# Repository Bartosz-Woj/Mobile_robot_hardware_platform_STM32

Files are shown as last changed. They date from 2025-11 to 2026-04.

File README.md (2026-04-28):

# Mobile robot hardware platform

## Project Description

**Universal PCB** with STM32G431 with two 2 h-bridges and input/output connectors designed for usage as mobile robot mainboard. The PCB can be use as mainboard for mini sumo robot, balancing robot, linefollower and other similar projects.

## Main functionality

- high range of power suply voltage (recommended: 9-12V PSU or 2S-3S Li-Po)
- STM32G431
- IR receiver
- power lines: 3V3, 5V, 6V5 with step-down converters.
- switch for enabling/disabling power lines
- 2x i2C connector
- 2x servo connector
- 2x encoder connector
- 2x H-bridge (3.6A each)
- 2x 10pin IDC connector
- 1x 16pin IDC connector [for IR distance sensor](https://github.com/Bartosz-Woj/Modulated_infrared_distance_sensor)
- connector for IR sumo [robot start module](https://p1r.se/startmodule/)

## Program uploading and debugging

The ST-link can be connected to the J2 connector by IDC wire to [ST-Link Nucleo board programming shield] (https://github.com/Bartosz-Woj/ST_LINK-Nucleo-programming-shield) or to the connector J6 by goldpin wires.

## Software

In the folder /software there are example projects made in STM32CubeIDE which can be used for hardware testing and for initial configuration:

- initial_configuration - project with initial configuration of CubeMX. In the main function there is code for testing PWM.

## Project status

- electronic desing: finished
- example usage design: on going

## Additional modules

- [ST-Link Nucleo board programming shield](https://github.com/Bartosz-Woj/ST_LINK-Nucleo-programming-shield)
- [Modulated infrared distance sensor module which peak detection](https://github.com/Bartosz-Woj/Modulated_infrared_distance_sensor)

## Usage in mobile robot projects

- [Low cost mini sumo robot](https://github.com/Bartosz-Woj/Mini-sumo-robot)

## Photos

- **Schematic:**  
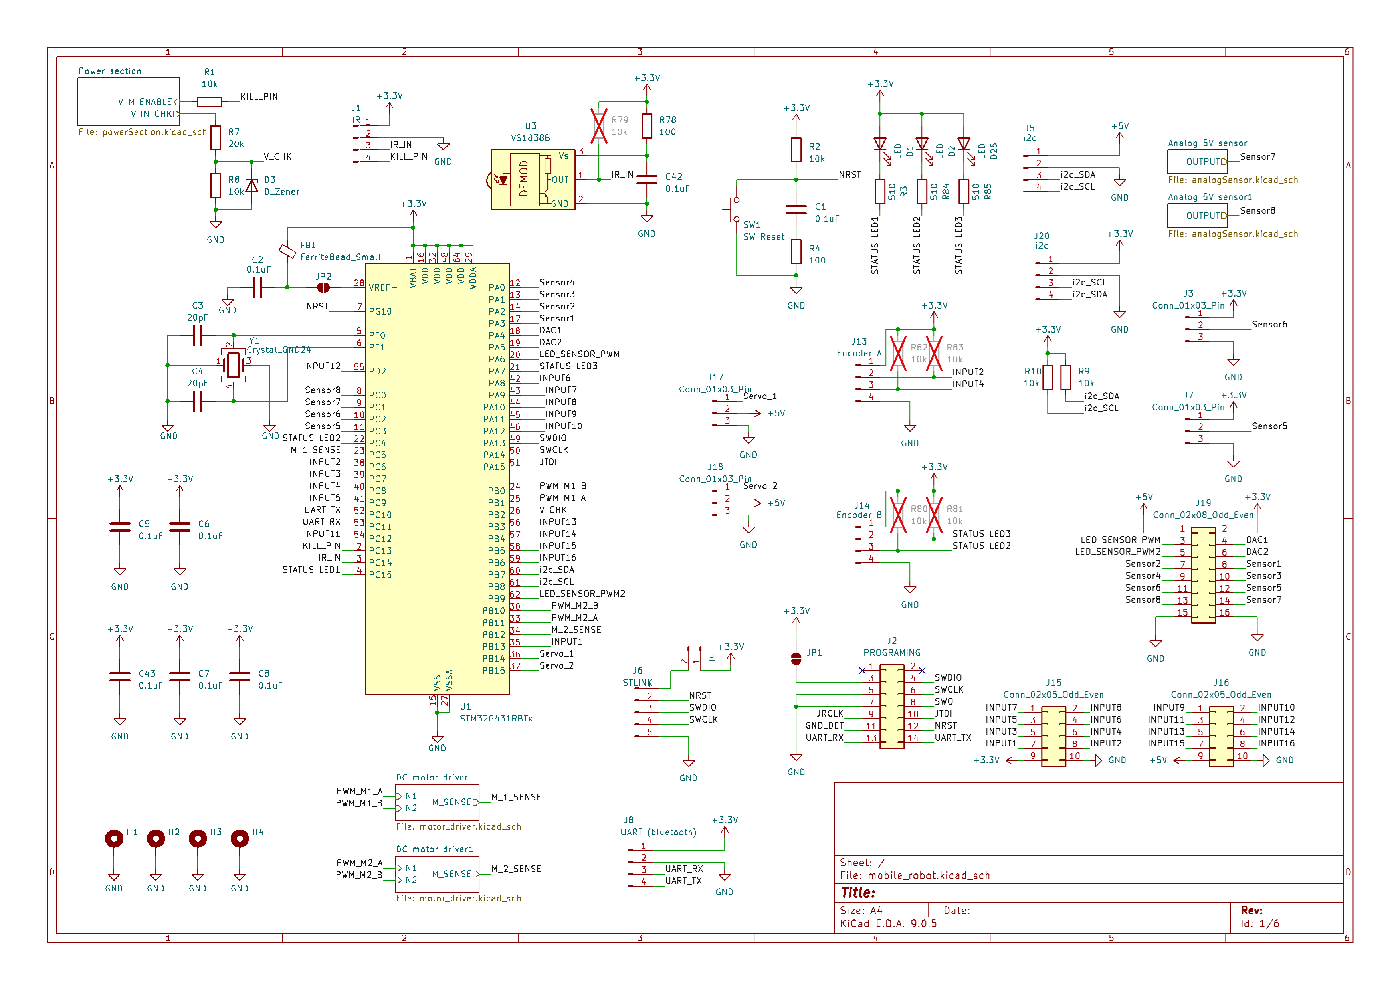
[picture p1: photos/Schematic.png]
Schematic
  
- **PCB top side:**  
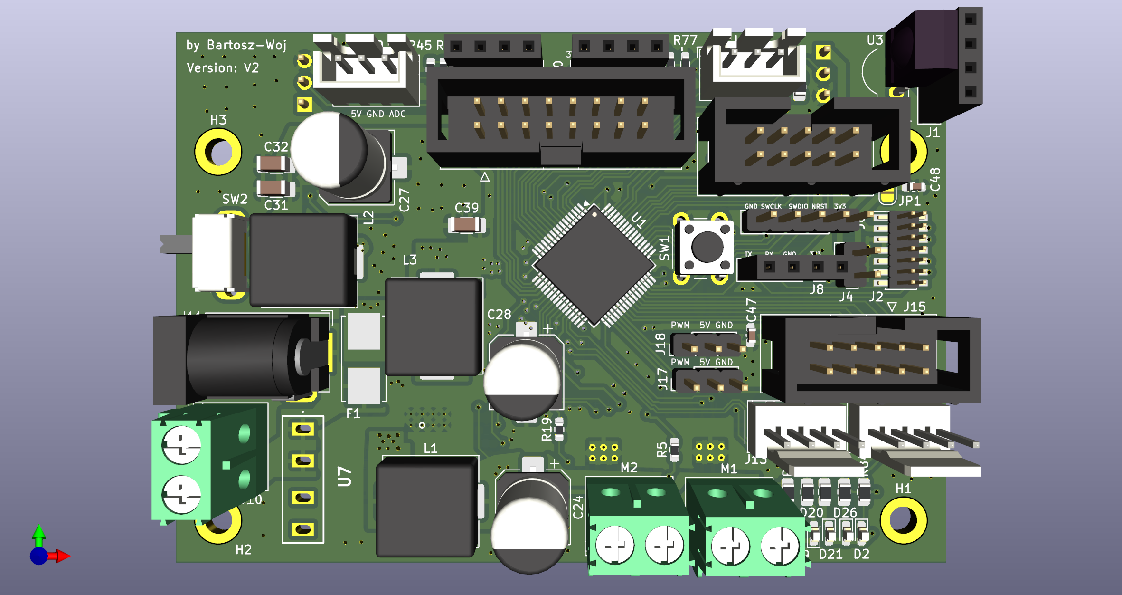
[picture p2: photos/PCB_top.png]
PCB top side
  
- **PCB bottom side:**  
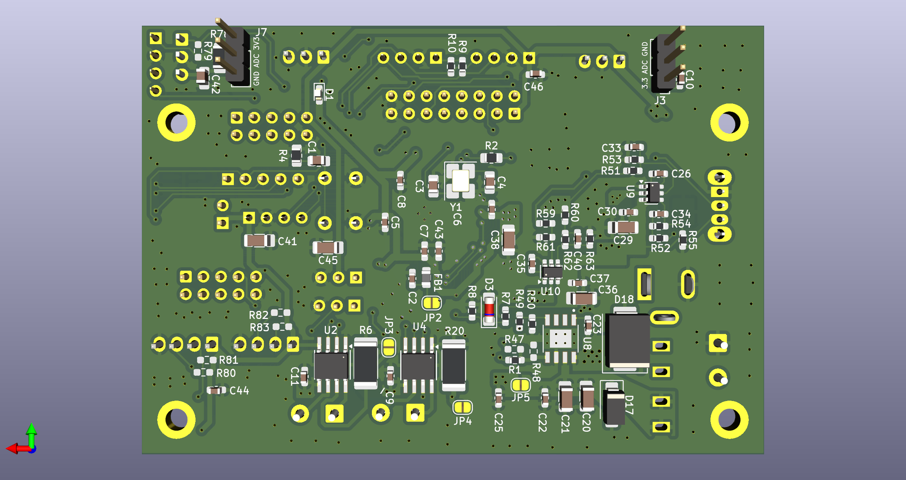
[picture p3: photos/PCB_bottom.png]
PCB bottom side
  

- **Debuging mode:**  
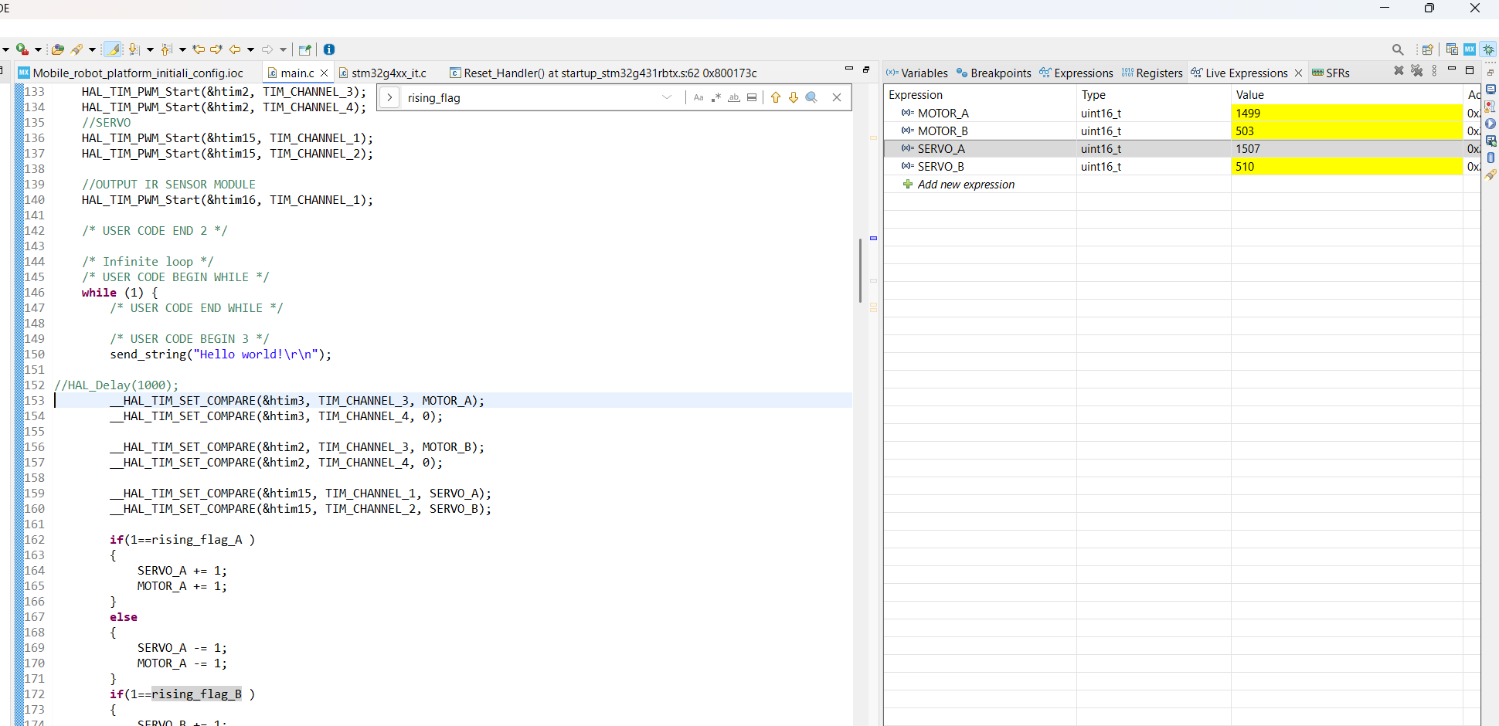
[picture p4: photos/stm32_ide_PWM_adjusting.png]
Debuging mode in STM32CubeIDE
  

- **Example connection with motors**  
  Connection with motors

---

## Author

- **Project by:** Bartosz-Woj (Bartosz Wojciechowski)
- **Date:** 10.11.2025

---

## License

Licensed under the **CERN Open Hardware License v2 – Permissive (CERN-OHL-P)**  
You are free to **use, modify, and redistribute** this project, provided that you **credit the original author**.

## Changelog

- V1 - initial release
- V2 - minor improvments: modified U3 footprint, rotated J7, updated routing (microcontroller, power section)

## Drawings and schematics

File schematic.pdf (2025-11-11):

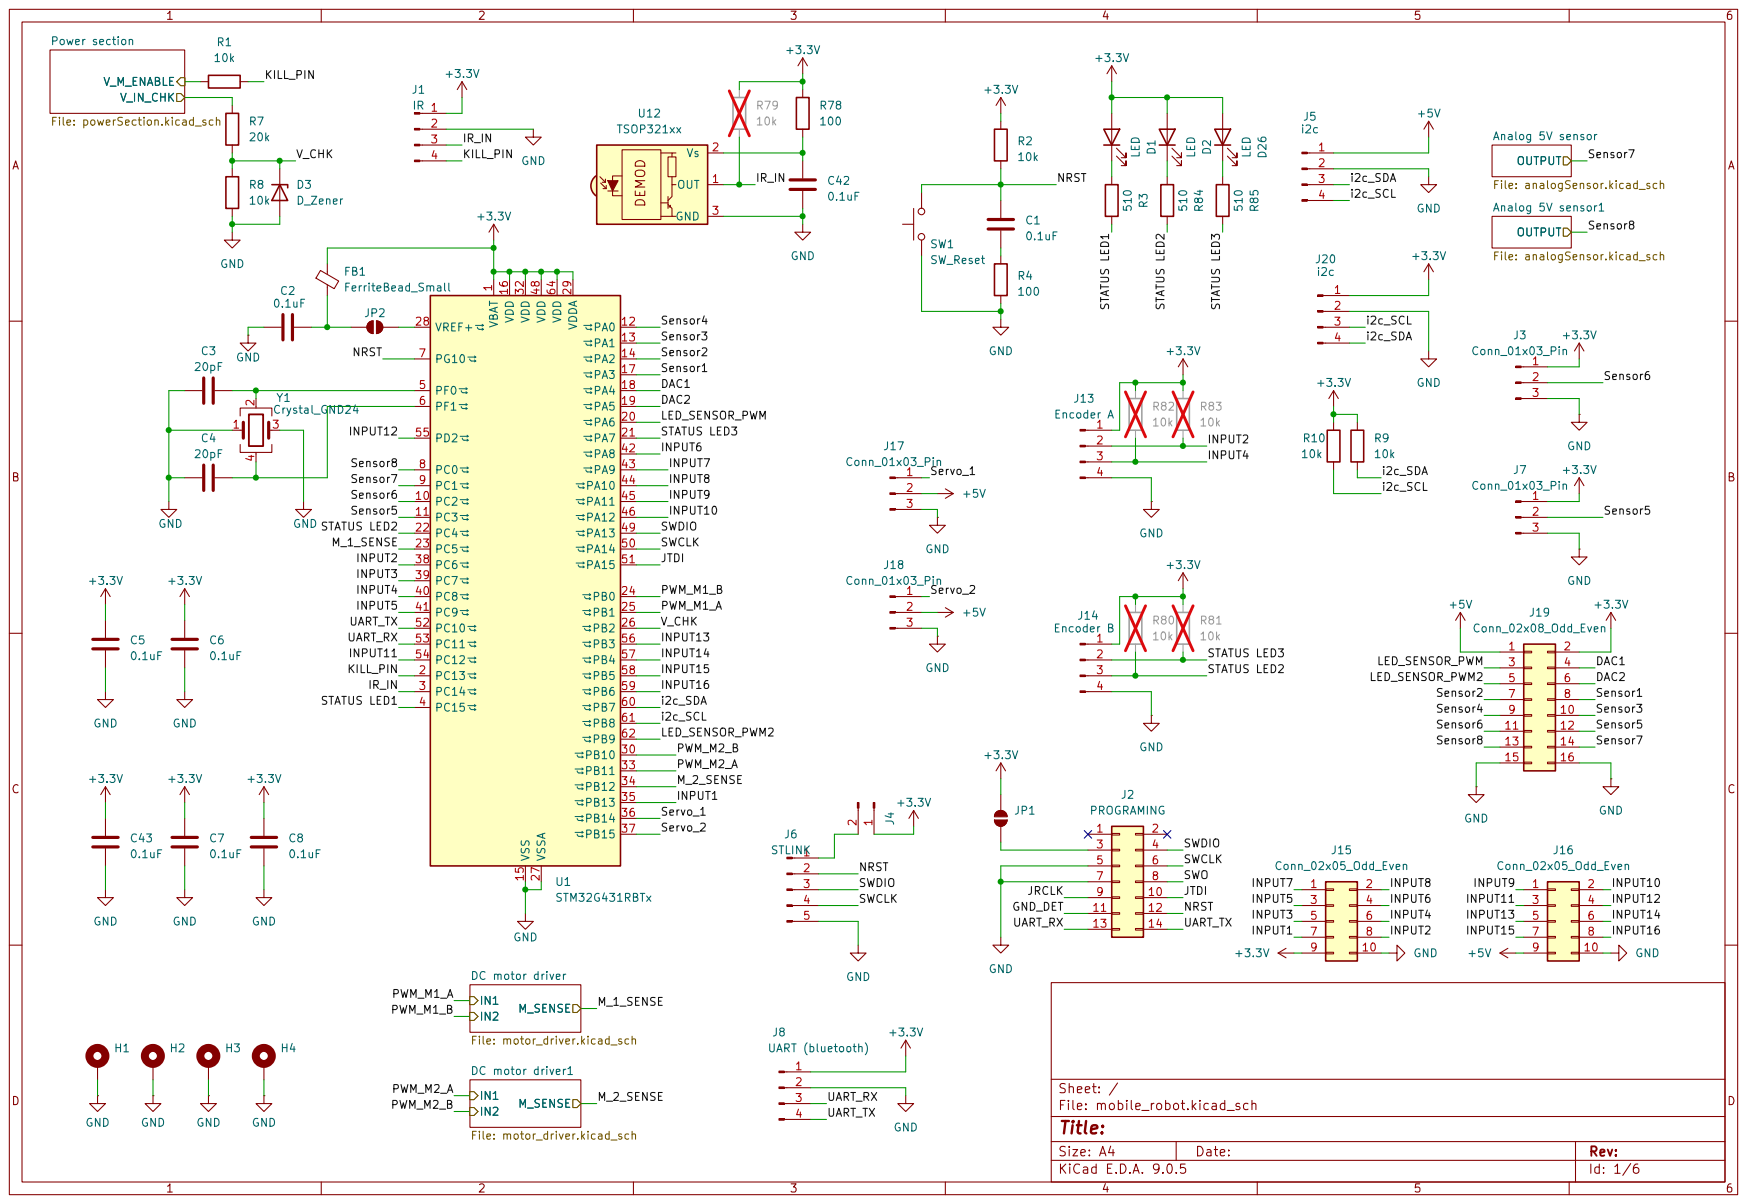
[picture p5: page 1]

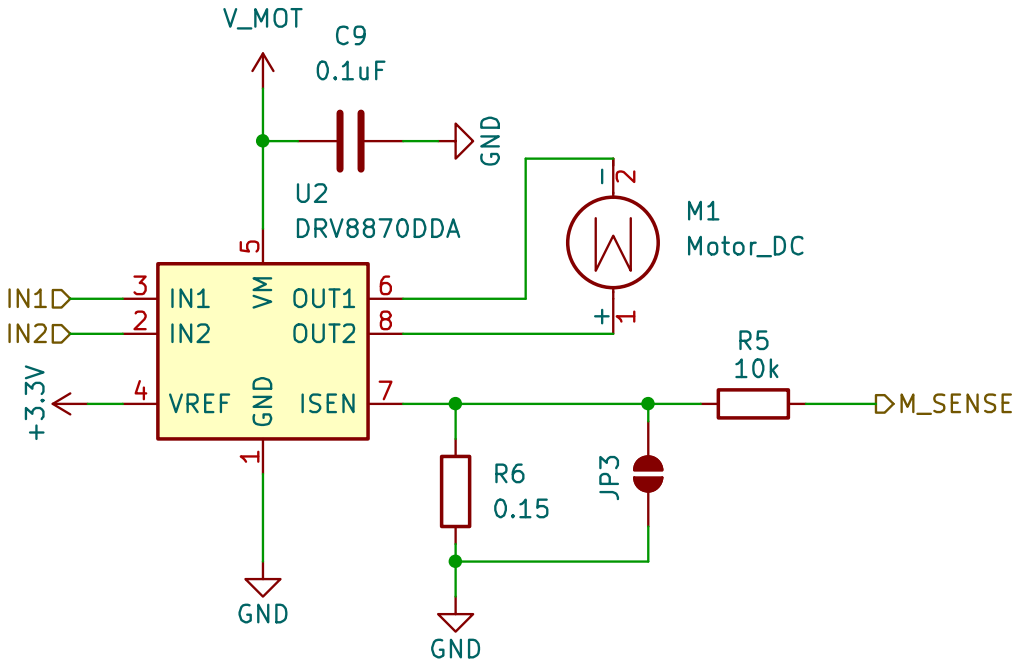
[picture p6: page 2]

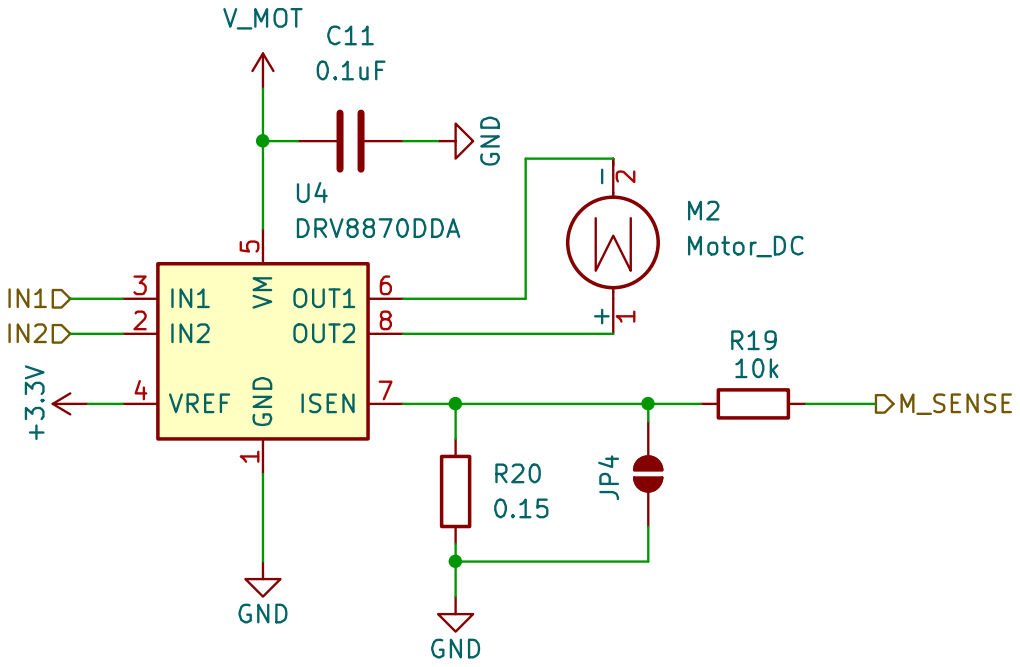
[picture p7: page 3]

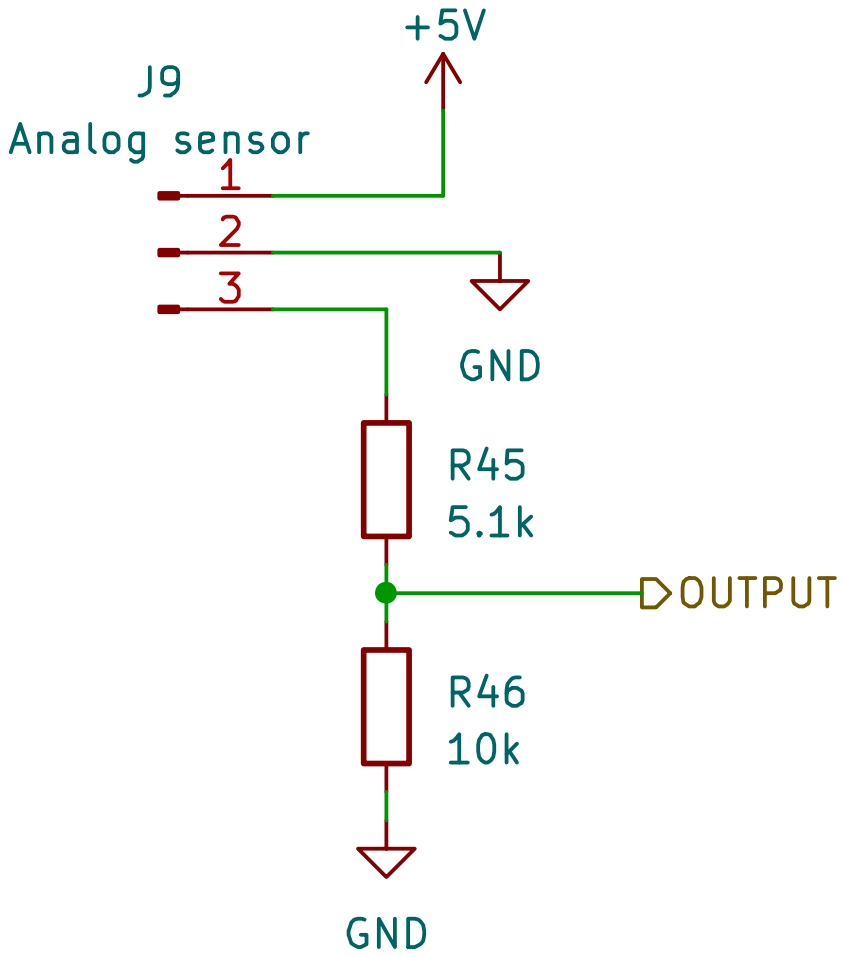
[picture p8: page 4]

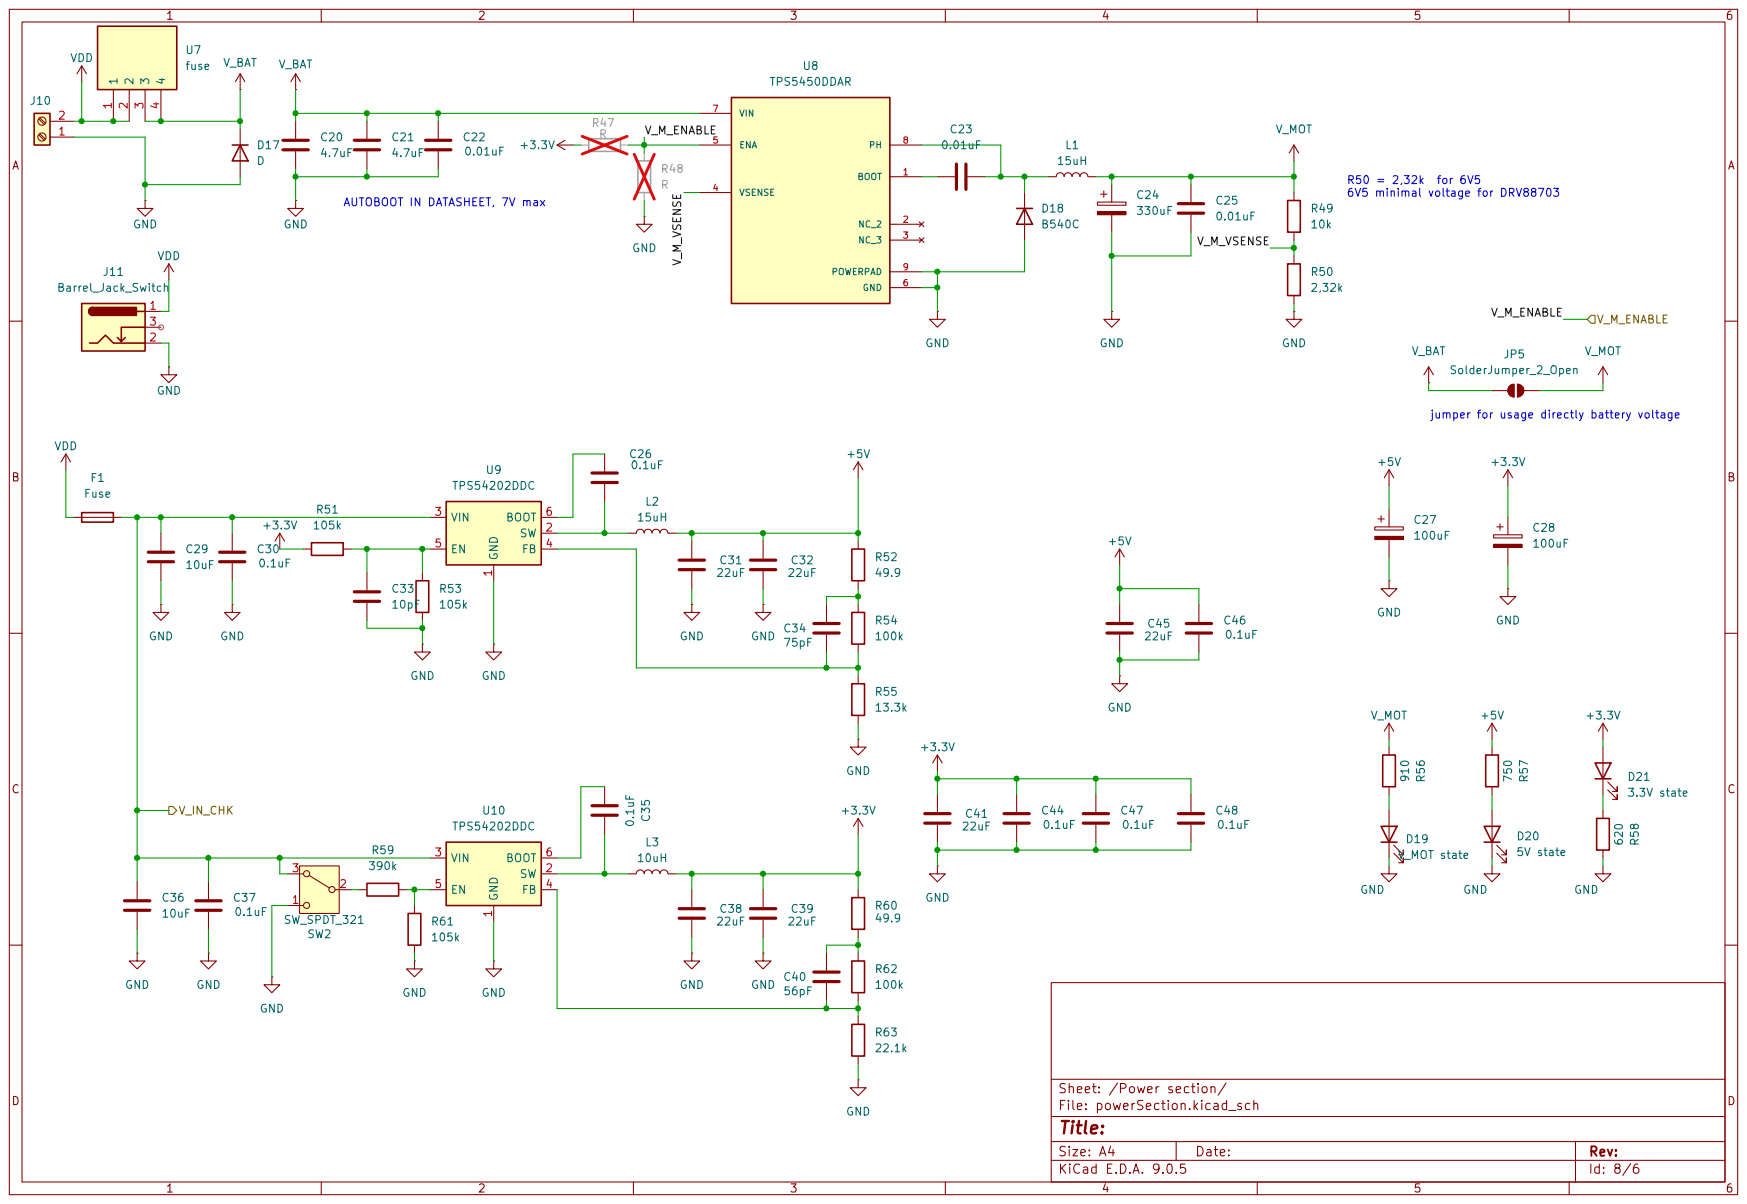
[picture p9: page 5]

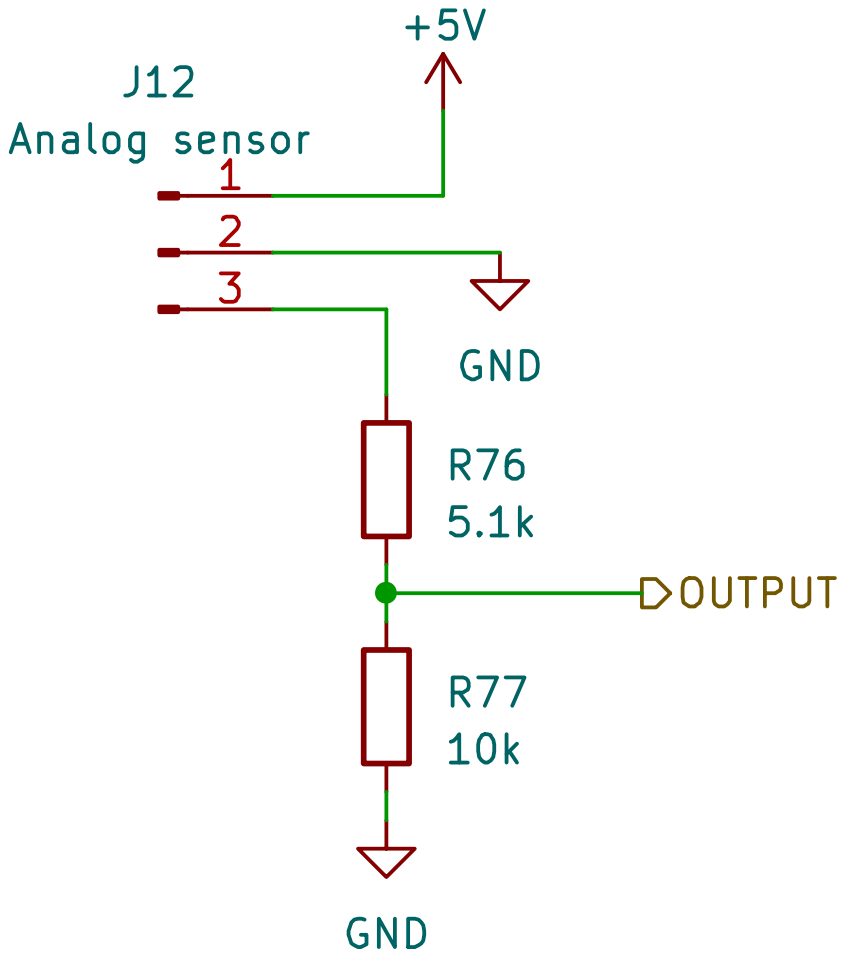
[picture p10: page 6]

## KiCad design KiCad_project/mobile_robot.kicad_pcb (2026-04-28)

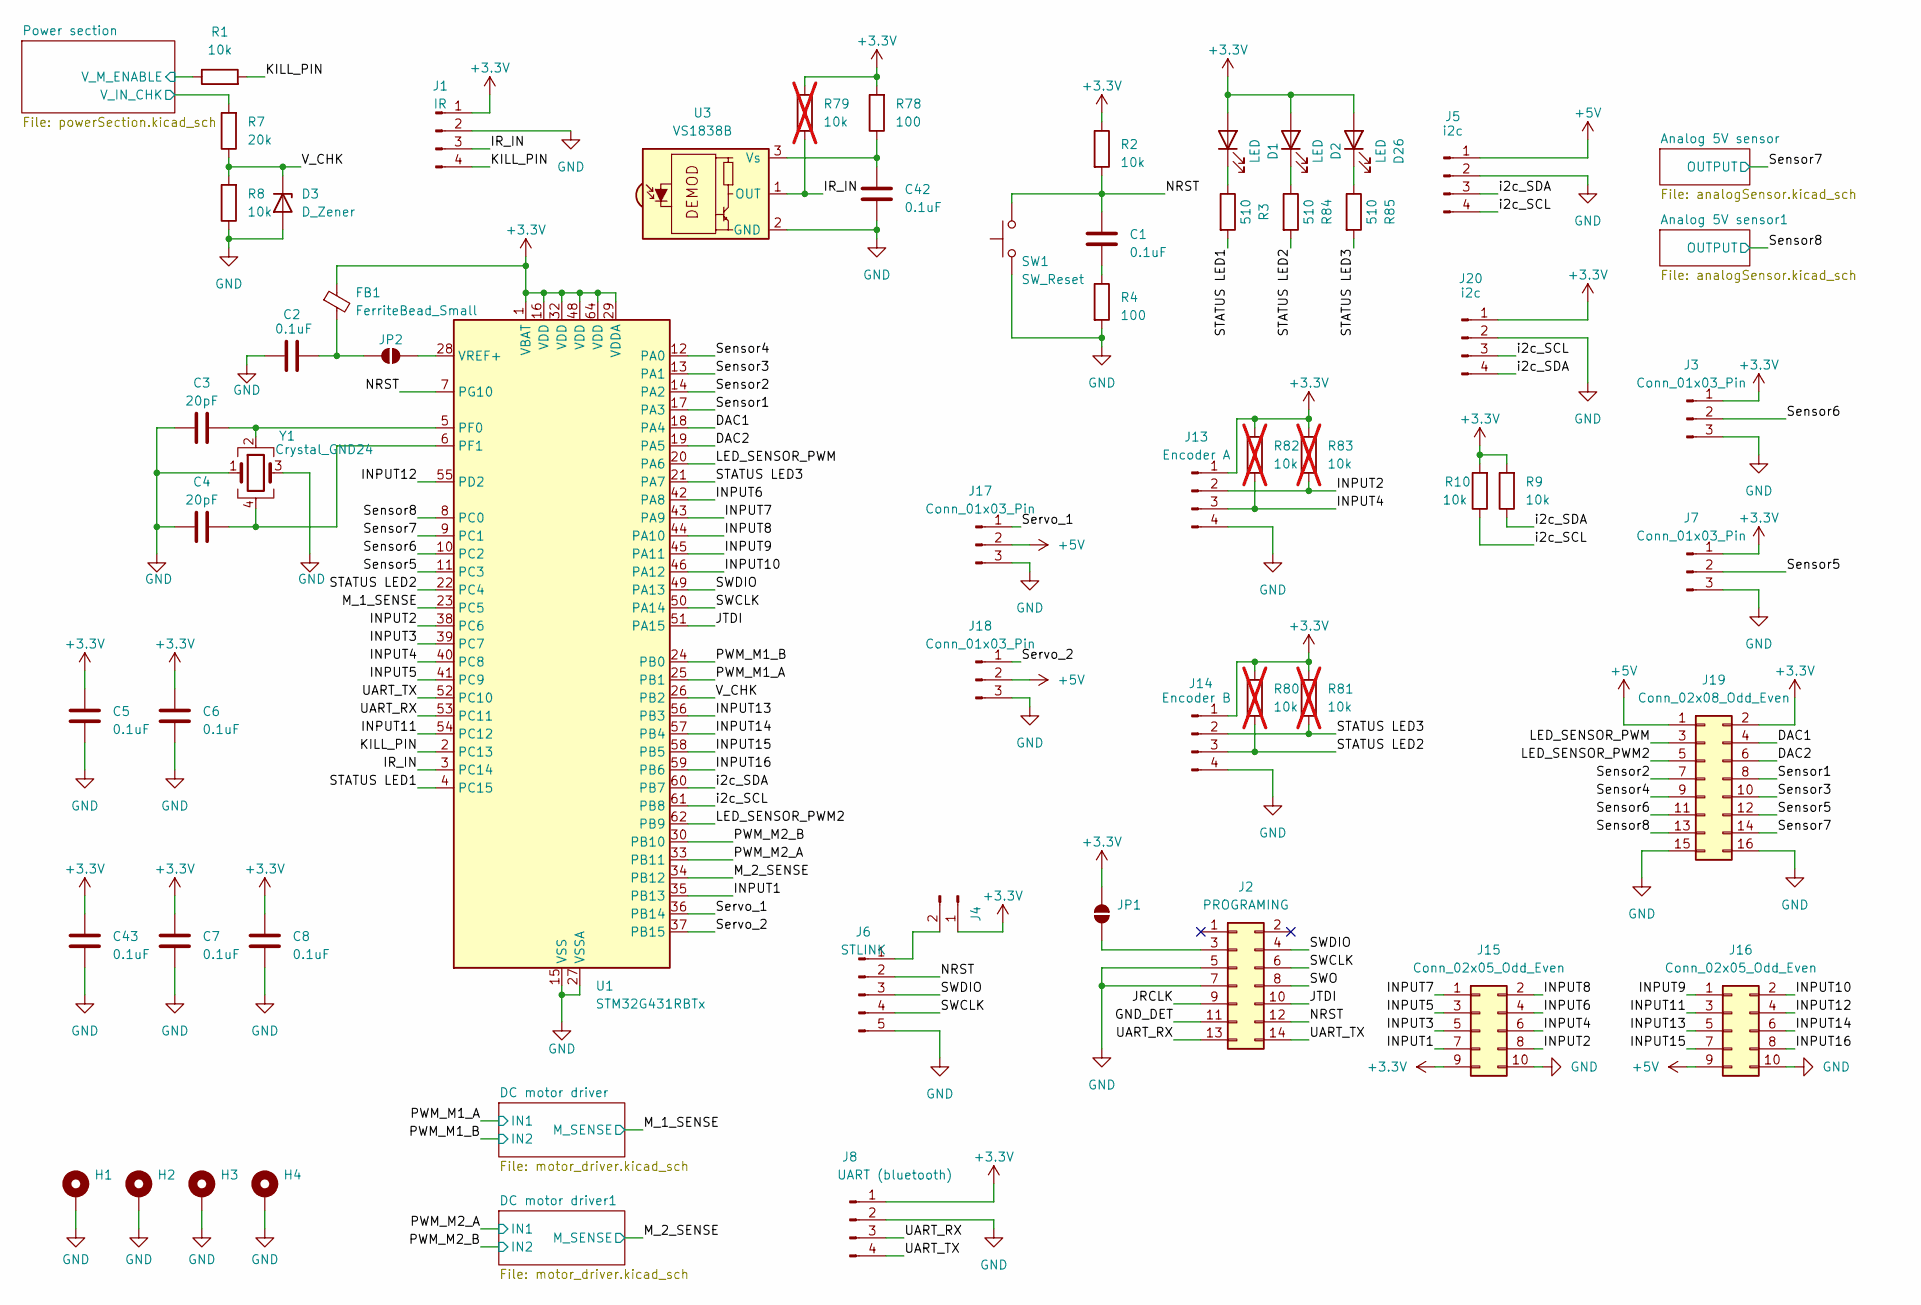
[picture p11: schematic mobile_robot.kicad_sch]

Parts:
C1, C42: 0.1uF; C_0805_2012Metric_Pad1.18x1.45mm_HandSolder
C2, C5, C6, C7, C8, C43: 0.1uF; C_0603_1608Metric_Pad1.08x0.95mm_HandSolder
C3, C4: 20pF; C_0805_2012Metric_Pad1.18x1.45mm_HandSolder
D1, D2, D26: LED; LED_0603_1608Metric_Pad1.05x0.95mm_HandSolder
D3: D_Zener; D_MiniMELF
FB1: FerriteBead_Small; L_0805_2012Metric
H1, H2, H3, H4: MountingHole_Pad; MountingHole_3.2mm_M3_ISO14580_Pad
J1: IR; PinSocket_1x04_P2.54mm_Vertical
J2: PROGRAMING; PinHeader_2x07_P1.27mm_Vertical_SMD
J3, J7, J17, J18: Conn_01x03_Pin; PinHeader_1x03_P2.54mm_Vertical
J4: Conn_01x02_Pin; PinHeader_1x02_P2.54mm_Vertical
J5, J20: i2c; PinSocket_1x04_P2.54mm_Vertical
J6: STLINK; PinHeader_1x05_P2.54mm_Vertical
J8: UART (bluetooth); PinSocket_1x04_P2.54mm_Vertical
J13: Encoder A; Molex_KK-254_AE-6410-04A_1x04_P2.54mm_Vertical
J14: Encoder B; Molex_KK-254_AE-6410-04A_1x04_P2.54mm_Vertical
J15, J16: Conn_02x05_Odd_Even; IDC-Header_2x05_P2.54mm_Vertical
J19: Conn_02x08_Odd_Even; IDC-Header_2x08_P2.54mm_Vertical
JP1, JP2: SolderJumper_2_Open; SolderJumper-2_P1.3mm_Open_RoundedPad1.0x1.5mm
R1, R8, R9, R10: 10k; R_0603_1608Metric_Pad0.98x0.95mm_HandSolder
R2: 10k; R_0805_2012Metric_Pad1.20x1.40mm_HandSolder
R3, R84, R85: 510; R_0805_2012Metric_Pad1.20x1.40mm_HandSolder
R4: 100; R_0805_2012Metric_Pad1.20x1.40mm_HandSolder
R7: 20k; R_0603_1608Metric_Pad0.98x0.95mm_HandSolder
R78: 100; R_1206_3216Metric_Pad1.30x1.75mm_HandSolder
R79, R80, R81, R82, R83: 10k; R_0603_1608Metric_Pad0.98x0.95mm_HandSolder; not fitted
SW1: SW_Reset; SW_PUSH_6mm
U1: STM32G431RBTx; LQFP-64_10x10mm_P0.5mm
U3: VS1838B; Vishay_MOLD-3Pin
Y1: Crystal_GND24; Crystal_SMD_3225-4Pin_3.2x2.5mm_HandSoldering

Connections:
+3.3V: C5.1, C6.1, C7.1, C8.1, C43.1, D1.2 (A), D2.2 (A), D26.2 (A), FB1.1, J1.1, J3.1, J4.1, J7.1, J8.1, J13.1, J14.1, J15.9, J19.2, J20.1, JP1.2 (B), R2.1, R9.2, R10.2, R78.2, R79.2, R80.1, R81.1, R82.1, R83.1, U1.1 (VBAT), U1.16 (VDD), U1.29 (VDDA), U1.32 (VDD), U1.48 (VDD), U1.64 (VDD); also elsewhere on the board
+5V: J5.1, J16.9, J17.2, J18.2, J19.1; also elsewhere on the board
/DAC1: J19.4, U1.18 (PA4)
/DAC2: J19.6, U1.19 (PA5)
/GND_DET: J2.11
/INPUT1: J15.7, U1.35 (PB13)
/INPUT2: J13.2, J15.8, R83.2, U1.38 (PC6)
/INPUT3: J15.5, U1.39 (PC7)
/INPUT4: J13.3, J15.6, R82.2, U1.40 (PC8)
/INPUT5: J15.3, U1.41 (PC9)
/INPUT6: J15.4, U1.42 (PA8)
/INPUT7: J15.1, U1.43 (PA9)
/INPUT8: J15.2, U1.44 (PA10)
/INPUT9: J16.1, U1.45 (PA11)
/INPUT10: J16.2, U1.46 (PA12)
/INPUT11: J16.3, U1.54 (PC12)
/INPUT12: J16.4, U1.55 (PD2)
/INPUT13: J16.5, U1.56 (PB3)
/INPUT14: J16.6, U1.57 (PB4)
/INPUT15: J16.7, U1.58 (PB5)
/INPUT16: J16.8, U1.59 (PB6)
/IR_IN: J1.3, R79.1, U1.3 (PC14), U3.1 (OUT)
/JRCLK: J2.9
/JTDI: J2.10, U1.51 (PA15)
/KILL_PIN: J1.4, R1.2, U1.2 (PC13)
/LED_SENSOR_PWM: J19.3, U1.20 (PA6)
/LED_SENSOR_PWM2: J19.5, U1.62 (PB9)
/M_1_SENSE: U1.23 (PC5); also elsewhere on the board
/M_2_SENSE: U1.34 (PB12); also elsewhere on the board
/NRST: C1.1, J2.12, J6.2, R2.2, SW1.2, U1.7 (PG10)
/PWM_M1_A: U1.25 (PB1); also elsewhere on the board
/PWM_M1_B: U1.24 (PB0); also elsewhere on the board
/PWM_M2_A: U1.33 (PB11); also elsewhere on the board
/PWM_M2_B: U1.30 (PB10); also elsewhere on the board
/Power section/V_IN_CHK: R7.2; also elsewhere on the board
/Power section/V_M_ENABLE: R1.1; also elsewhere on the board
/STATUS LED1: R3.2, U1.4 (PC15)
/STATUS LED2: J14.3, R80.2, R84.2, U1.22 (PC4)
/STATUS LED3: J14.2, R81.2, R85.2, U1.21 (PA7)
/SWCLK: J2.6, J6.4, U1.50 (PA14)
/SWDIO: J2.4, J6.3, U1.49 (PA13)
/SWO: J2.8
/Sensor1: J19.8, U1.17 (PA3)
/Sensor2: J19.7, U1.14 (PA2)
/Sensor3: J19.10, U1.13 (PA1)
/Sensor4: J19.9, U1.12 (PA0)
/Sensor5: J7.2, J19.12, U1.11 (PC3)
/Sensor6: J3.2, J19.11, U1.10 (PC2)
/Sensor7: J19.14, U1.9 (PC1); also elsewhere on the board
/Sensor8: J19.13, U1.8 (PC0); also elsewhere on the board
/Servo_1: J17.1, U1.36 (PB14)
/Servo_2: J18.1, U1.37 (PB15)
/UART_RX: J2.13, J8.3, U1.53 (PC11)
/UART_TX: J2.14, J8.4, U1.52 (PC10)
/V_CHK: D3.1 (K), R7.1, R8.2, U1.26 (PB2)
/i2c_SCL: J5.4, J20.3, R10.1, U1.61 (PB8)
/i2c_SDA: J5.3, J20.4, R9.1, U1.60 (PB7)
GND: C2.1, C3.2, C4.2, C5.2, C6.2, C7.2, C8.2, C42.2, C43.2, D3.2 (A), H1.1, H2.1, H3.1, H4.1, J1.2, J2.5, J2.7, J3.3, J5.2, J6.5, J7.3, J8.2, J13.4, J14.4, J15.10, J16.10, J17.3, J18.3, J19.15, J19.16, J20.2, R4.2, R8.1, SW1.1, U1.15 (VSS), U1.27 (VSSA), U1.31 (VSS), U1.47 (VSS), U1.63 (VSS), U3.2 (GND), Y1.1, Y1.3; also elsewhere on the board
unnamed: C1.2, R4.1
unnamed: D1.1 (K), R3.1
unnamed: D2.1 (K), R84.1
unnamed: D26.1 (K), R85.1
unnamed: J2.3, JP1.1 (A)
unnamed: J4.2, J6.1
unnamed: C2.2, FB1.2, JP2.1 (A)
unnamed: JP2.2 (B), U1.28 (VREF+)
unnamed: C3.1, U1.5 (PF0), Y1.2
unnamed: C4.1, U1.6 (PF1), Y1.4
unnamed: C42.1, R78.1, U3.3 (Vs)

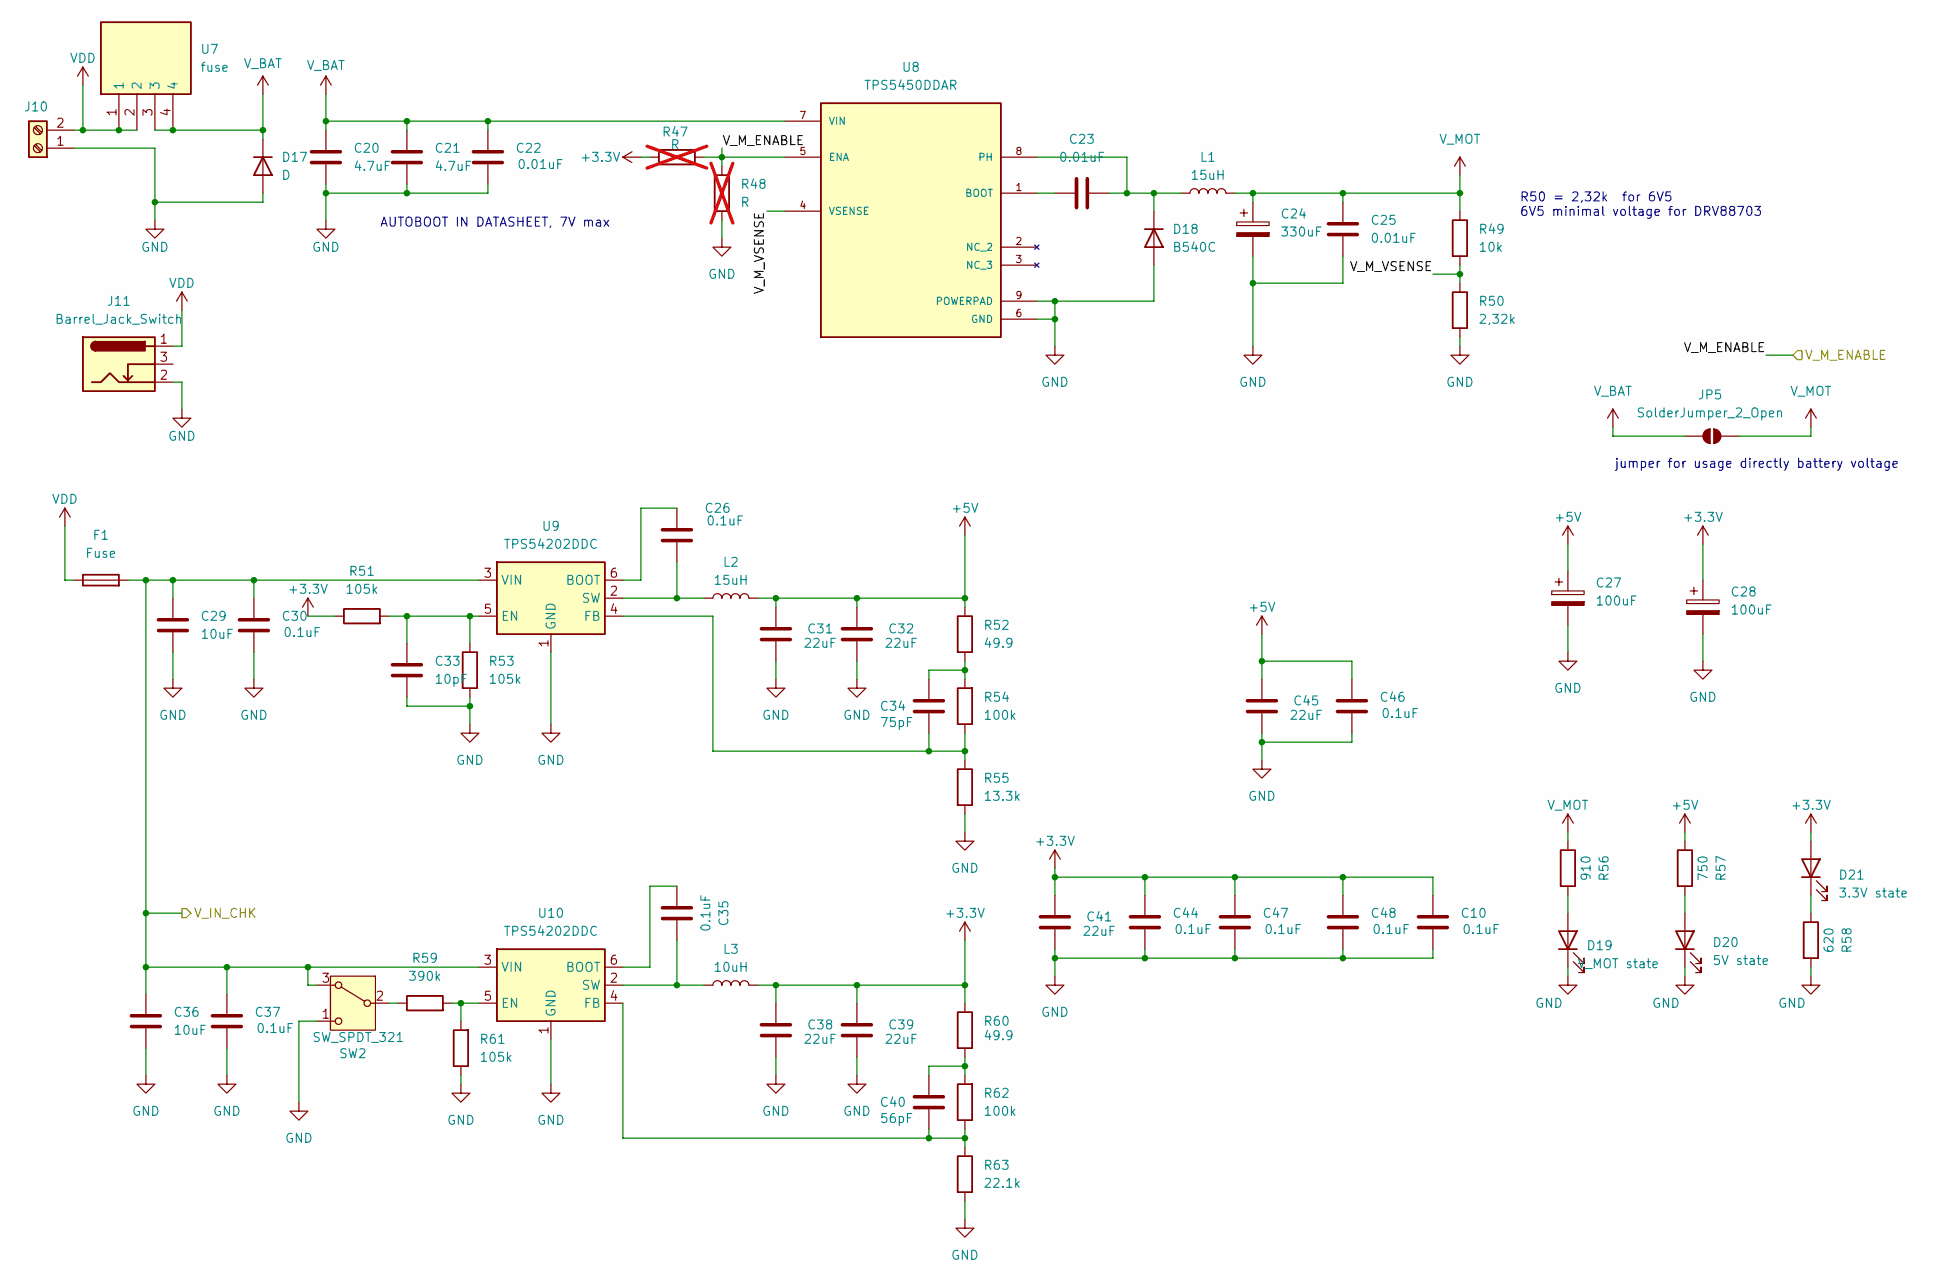
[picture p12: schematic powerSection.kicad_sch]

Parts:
C10, C26, C30, C35, C37, C44, C46, C47, C48: 0.1uF; C_0603_1608Metric_Pad1.08x0.95mm_HandSolder
C20, C21: 4.7uF; C_1206_3216Metric_Pad1.33x1.80mm_HandSolder
C22, C23, C25: 0.01uF; C_0603_1608Metric_Pad1.08x0.95mm_HandSolder
C24: 330uF; CP_Elec_8x10.5
C27, C28: 100uF; CP_Elec_8x10.5
C29, C36: 10uF; C_1206_3216Metric_Pad1.33x1.80mm_HandSolder
C31, C32, C38, C39, C41, C45: 22uF; C_1206_3216Metric_Pad1.33x1.80mm_HandSolder
C33: 10pF; C_0603_1608Metric_Pad1.08x0.95mm_HandSolder
C34: 75pF; C_0603_1608Metric_Pad1.08x0.95mm_HandSolder
C40: 56pF; C_0603_1608Metric_Pad1.08x0.95mm_HandSolder
D17: D; D_SMA
D18: B540C; D_SMC
D19: V_MOT state; LED_0603_1608Metric_Pad1.05x0.95mm_HandSolder
D20: 5V state; LED_0603_1608Metric_Pad1.05x0.95mm_HandSolder
D21: 3.3V state; LED_0603_1608Metric_Pad1.05x0.95mm_HandSolder
F1: Fuse; Fuseholder_Littelfuse_Nano2_154x
J10: Screw_Terminal_01x02; TerminalBlock_Phoenix_PT-1,5-2-5.0-H_1x02_P5.00mm_Horizontal
J11: Barrel_Jack_Switch; BarrelJack_GCT_DCJ200-10-A_Horizontal
JP5: SolderJumper_2_Open; SolderJumper-2_P1.3mm_Open_RoundedPad1.0x1.5mm
L1, L2: 15uH; L_TechFuse_SL1040
L3: 10uH; L_TechFuse_SL1040
R47, R48: R; R_0603_1608Metric_Pad0.98x0.95mm_HandSolder; not fitted
R49: 10k; R_0603_1608Metric_Pad0.98x0.95mm_HandSolder
R50: 2,32k; R_0603_1608Metric_Pad0.98x0.95mm_HandSolder
R51, R53, R61: 105k; R_0603_1608Metric_Pad0.98x0.95mm_HandSolder
R52, R60: 49.9; R_0603_1608Metric_Pad0.98x0.95mm_HandSolder
R54, R62: 100k; R_0603_1608Metric_Pad0.98x0.95mm_HandSolder
R55: 13.3k; R_0603_1608Metric_Pad0.98x0.95mm_HandSolder
R56: 910; R_0805_2012Metric_Pad1.20x1.40mm_HandSolder
R57: 750; R_0805_2012Metric_Pad1.20x1.40mm_HandSolder
R58: 620; R_0805_2012Metric_Pad1.20x1.40mm_HandSolder
R59: 390k; R_0603_1608Metric_Pad0.98x0.95mm_HandSolder
R63: 22.1k; R_0603_1608Metric_Pad0.98x0.95mm_HandSolder
SW2: SW_SPDT_321; SW_Slide_SPDT_Angled_CK_OS102011MA1Q
U7: fuse; 01000063Zfuse; Manufacturer_Part_Number 01000063Z; Mouser Part Number 576-01000063Z
U8: TPS5450DDAR; CONV_TPS5450DDAR; PARTREV D
U9, U10: TPS54202DDC; SOT-23-6

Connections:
+3.3V: C10.1, C28.1, C38.1, C39.1, C41.1, C44.1, C47.1, C48.1, D21.2 (A), L3.2, R47.1, R51.1, R60.1; also elsewhere on the board
+5V: C27.1, C31.1, C32.1, C45.1, C46.1, L2.2, R52.1, R57.1; also elsewhere on the board
/Power section/V_IN_CHK: C29.1, C30.1, C36.1, C37.1, F1.2, SW2.3 (A), U9.3 (VIN), U10.3 (VIN); also elsewhere on the board
/Power section/V_M_ENABLE: R47.2, R48.2, U8.5 (ENA); also elsewhere on the board
/Power section/V_M_VSENSE: R49.2, R50.1, U8.4 (VSENSE)
GND: C10.2, C20.2, C21.2, C22.2, C24.2, C25.2, C27.2, C28.2, C29.2, C30.2, C31.2, C32.2, C33.2, C36.2, C37.2, C38.2, C39.2, C41.2, C44.2, C45.2, C46.2, C47.2, C48.2, D17.2 (A), D18.2 (A), D19.1 (K), D20.1 (K), J10.1, J11.2, R48.1, R50.2, R53.2, R55.2, R58.2, R61.1, R63.2, SW2.1 (C), U8.6 (GND), U8.9 (POWERPAD), U9.1 (GND), U10.1 (GND); also elsewhere on the board
unnamed: C34.2, R52.2, R54.2
unnamed: C40.2, R60.2, R62.2
unnamed: C23.2, D18.1 (K), L1.1, U8.8 (PH)
unnamed: D19.2 (A), R56.2
unnamed: D20.2 (A), R57.2
unnamed: D21.1 (K), R58.1
unnamed: R59.1, SW2.2 (B)
unnamed: C23.1, U8.1 (BOOT)
unnamed: C26.1, U9.6 (BOOT)
unnamed: C33.1, R51.2, R53.1, U9.5 (EN)
unnamed: C34.1, R54.1, R55.1, U9.4 (FB)
unnamed: C26.2, L2.1, U9.2 (SW)
unnamed: C35.1, U10.6 (BOOT)
unnamed: R59.2, R61.2, U10.5 (EN)
unnamed: C40.1, R62.1, R63.1, U10.4 (FB)
unnamed: C35.2, L3.1, U10.2 (SW)
VDD: F1.1, J10.2, J11.1, U7.1, U7.2
V_BAT: C20.1, C21.1, C22.1, D17.1 (K), JP5.1 (A), U7.3, U7.4, U8.7 (VIN)
V_MOT: C24.1, C25.1, JP5.2 (B), L1.2, R49.1, R56.1; also elsewhere on the board

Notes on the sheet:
AUTOBOOT IN DATASHEET, 7V max
jumper for usage directly battery voltage
R50 = 2,32k for 6V5 6V5 minimal voltage for DRV88703

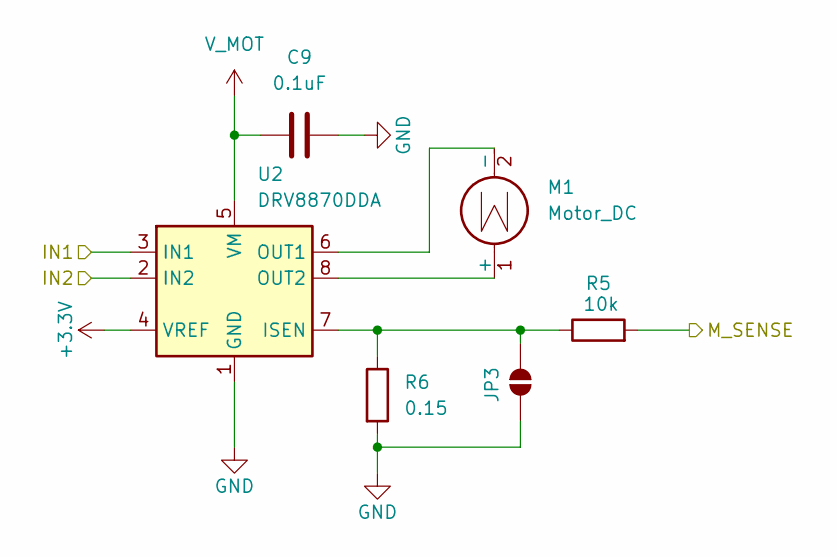
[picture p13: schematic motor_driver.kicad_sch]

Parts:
C9: 0.1uF; C_0603_1608Metric_Pad1.08x0.95mm_HandSolder
JP3: SolderJumper_2_Open; SolderJumper-2_P1.3mm_Open_RoundedPad1.0x1.5mm
M1: Motor_DC; TerminalBlock_Phoenix_PT-1,5-2-5.0-H_1x02_P5.00mm_Horizontal
R5: 10k; R_0603_1608Metric_Pad0.98x0.95mm_HandSolder
R6: 0.15; R_2512_6332Metric_Pad1.40x3.35mm_HandSolder
U2: DRV8870DDA; Texas_HTSOP-8-1EP_3.9x4.9mm_P1.27mm_EP2.95x4.9mm_Mask2.4x3.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

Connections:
+3.3V: U2.4 (VREF); also elsewhere on the board
/M_2_SENSE: R5.2; also elsewhere on the board
/PWM_M2_A: U2.3 (IN1); also elsewhere on the board
/PWM_M2_B: U2.2 (IN2); also elsewhere on the board
GND: C9.2, JP3.1 (A), R6.2, U2.1 (GND), U2.9 (GND); also elsewhere on the board
unnamed: JP3.2 (B), R5.1, R6.1, U2.7 (ISEN)
unnamed: M1.1 (+), U2.8 (OUT2)
unnamed: M1.2 (-), U2.6 (OUT1)
V_MOT: C9.1, U2.5 (VM); also elsewhere on the board

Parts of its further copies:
C11: 0.1uF; C_0603_1608Metric_Pad1.08x0.95mm_HandSolder
JP4: SolderJumper_2_Open; SolderJumper-2_P1.3mm_Open_RoundedPad1.0x1.5mm
M2: Motor_DC; TerminalBlock_Phoenix_PT-1,5-2-5.0-H_1x02_P5.00mm_Horizontal
R19: 10k; R_0603_1608Metric_Pad0.98x0.95mm_HandSolder
R20: 0.15; R_2512_6332Metric_Pad1.40x3.35mm_HandSolder
U4: DRV8870DDA; Texas_HTSOP-8-1EP_3.9x4.9mm_P1.27mm_EP2.95x4.9mm_Mask2.4x3.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

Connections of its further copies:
+3.3V: U4.4 (VREF); also elsewhere on the board
/M_1_SENSE: R19.2; also elsewhere on the board
/PWM_M1_A: U4.3 (IN1); also elsewhere on the board
/PWM_M1_B: U4.2 (IN2); also elsewhere on the board
GND: C11.2, JP4.1 (A), R20.2, U4.1 (GND), U4.9 (GND); also elsewhere on the board
unnamed: JP4.2 (B), R19.1, R20.1, U4.7 (ISEN)
unnamed: M2.1 (+), U4.8 (OUT2)
unnamed: M2.2 (-), U4.6 (OUT1)
V_MOT: C11.1, U4.5 (VM); also elsewhere on the board

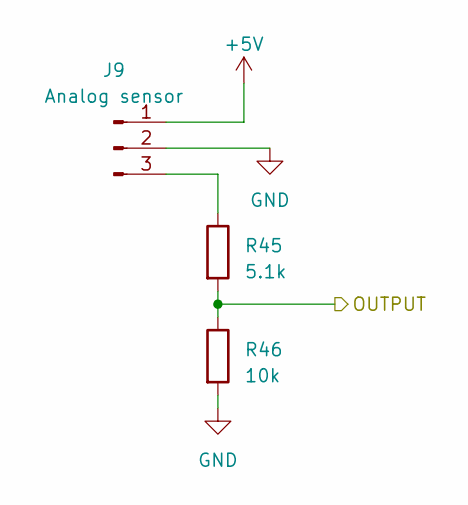
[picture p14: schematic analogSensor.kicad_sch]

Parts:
J9: Analog sensor; JST_XH_B3B-XH-A_1x03_P2.50mm_Vertical
R45: 5.1k; R_0603_1608Metric_Pad0.98x0.95mm_HandSolder
R46: 10k; R_0603_1608Metric_Pad0.98x0.95mm_HandSolder

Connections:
+5V: J9.1; also elsewhere on the board
/Sensor7: R45.2, R46.1; also elsewhere on the board
GND: J9.2, R46.2; also elsewhere on the board
unnamed: J9.3, R45.1

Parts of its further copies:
J12: Analog sensor; JST_XH_B3B-XH-A_1x03_P2.50mm_Vertical
R76: 5.1k; R_0603_1608Metric_Pad0.98x0.95mm_HandSolder
R77: 10k; R_0603_1608Metric_Pad0.98x0.95mm_HandSolder

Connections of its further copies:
+5V: J12.1; also elsewhere on the board
/Sensor8: R76.2, R77.1; also elsewhere on the board
GND: J12.2, R77.2; also elsewhere on the board
unnamed: J12.3, R76.1

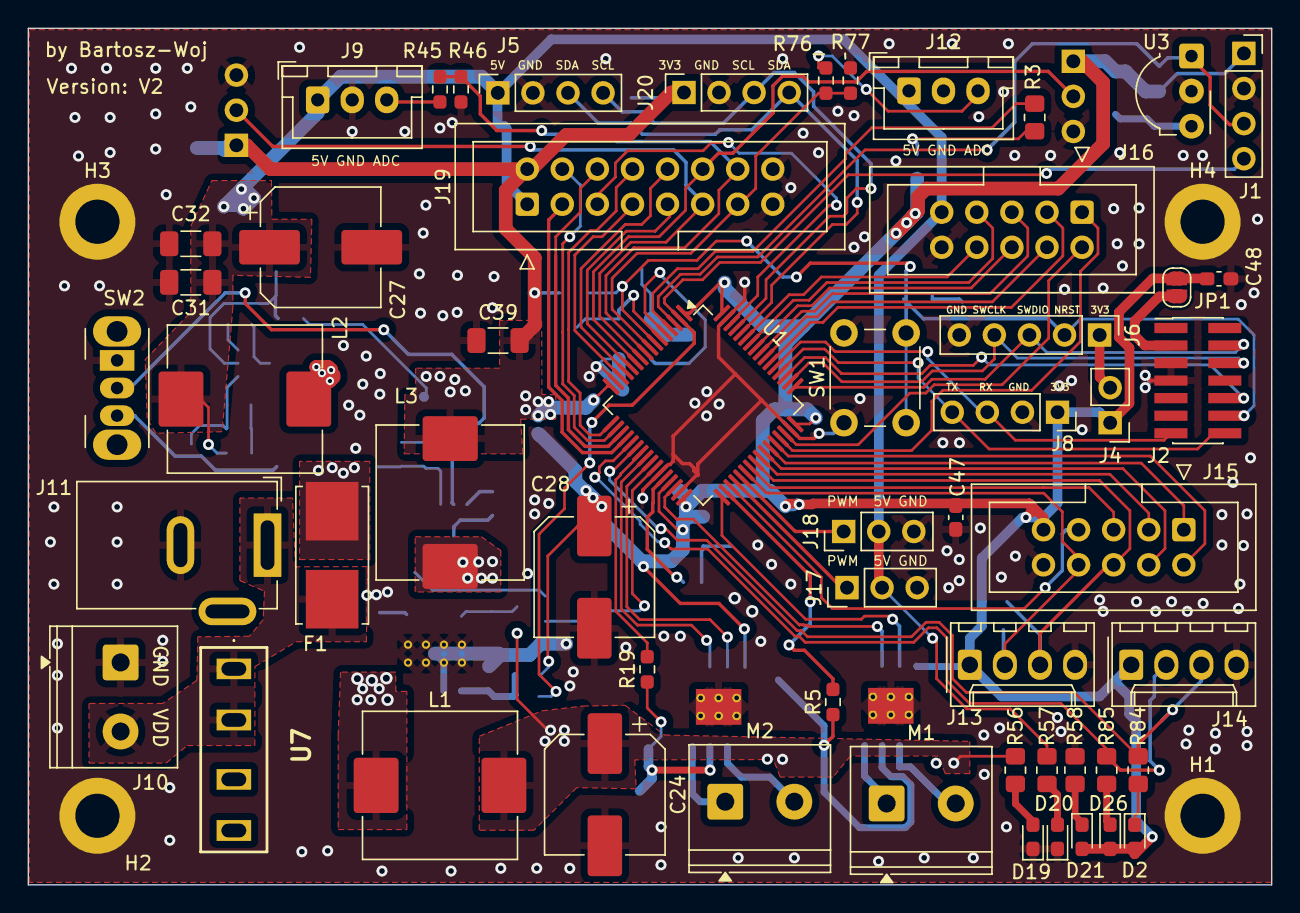
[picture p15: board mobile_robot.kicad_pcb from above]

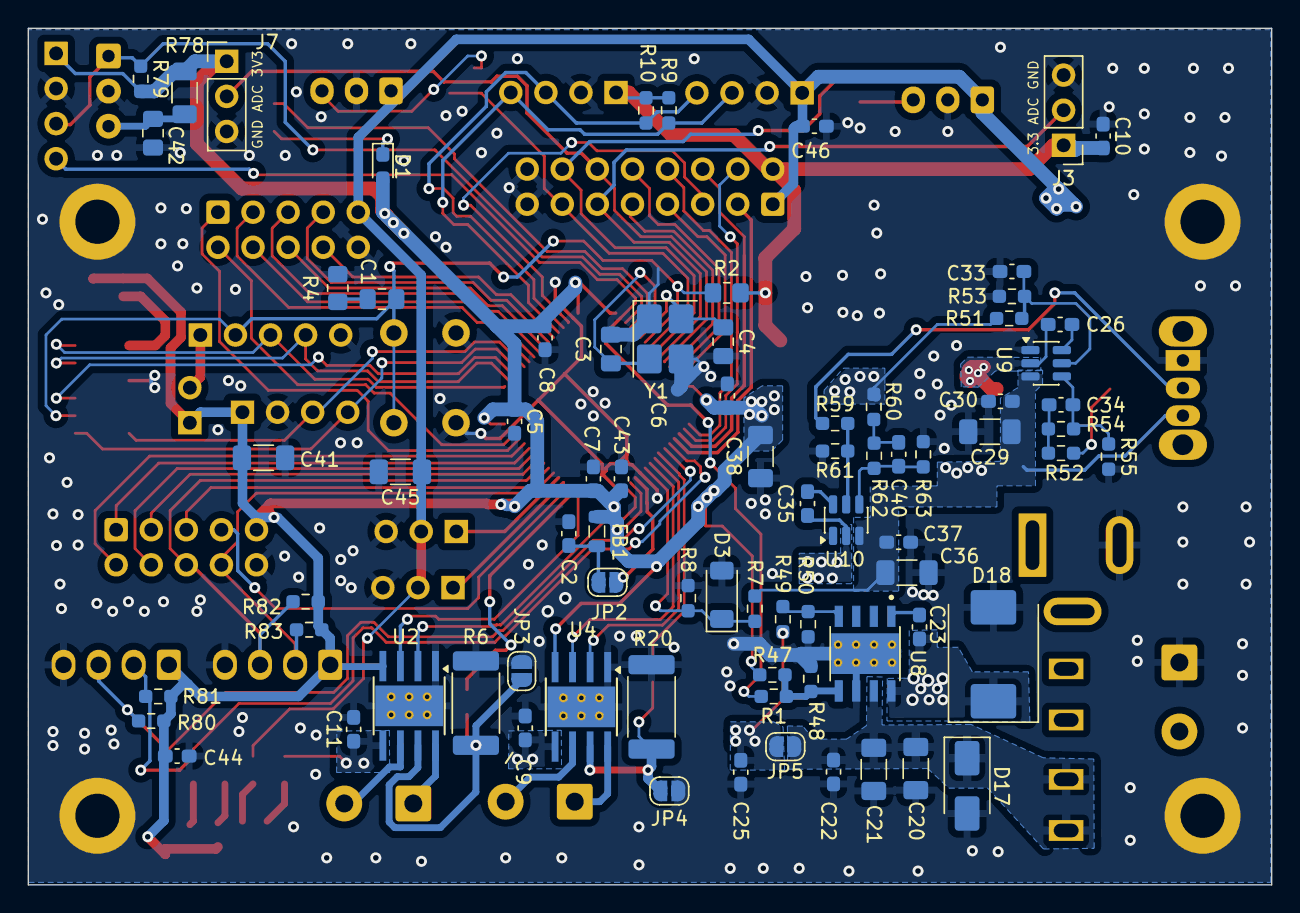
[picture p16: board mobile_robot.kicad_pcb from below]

Board: 2 copper layers, 90.0 x 62.0 mm, 137 parts (78 on the bottom side), 94 nets.

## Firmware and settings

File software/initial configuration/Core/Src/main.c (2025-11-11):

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
/* Includes ------------------------------------------------------------------*/
#include "main.h"

/* USER CODE BEGIN Includes */
#include <string.h>
/* USER CODE END Includes */

/* USER CODE BEGIN PTD */
uint16_t MOTOR_A = 1000;
uint16_t MOTOR_B = 0;

uint16_t SERVO_A = 1000;
uint16_t SERVO_B = 0;

uint8_t rising_flag_A = 1;
uint8_t rising_flag_B = 1;
/* USER CODE END PTD */

ADC_HandleTypeDef hadc1;
ADC_HandleTypeDef hadc2;

I2C_HandleTypeDef hi2c1;

TIM_HandleTypeDef htim2;
TIM_HandleTypeDef htim3;
TIM_HandleTypeDef htim15;
TIM_HandleTypeDef htim16;
TIM_HandleTypeDef htim17;

UART_HandleTypeDef huart3;

void SystemClock_Config(void);
static void MX_GPIO_Init(void);
static void MX_ADC2_Init(void);
static void MX_ADC1_Init(void);
static void MX_I2C1_Init(void);
static void MX_TIM17_Init(void);
static void MX_USART3_UART_Init(void);
static void MX_TIM3_Init(void);
static void MX_TIM15_Init(void);
static void MX_TIM16_Init(void);
static void MX_TIM2_Init(void);
/* USER CODE BEGIN 0 */
void send_string(char *s) {
	HAL_UART_Transmit(&huart3, (uint8_t*) s, strlen(s), 1000);
}
/* USER CODE END 0 */

/**
 * @brief  The application entry point.
 * @retval int
 */
int main(void) {

	/* MCU Configuration--------------------------------------------------------*/

	/* Reset of all peripherals, Initializes the Flash interface and the Systick. */
	HAL_Init();

	/* Configure the system clock */
	SystemClock_Config();

	/* Initialize all configured peripherals */
	MX_GPIO_Init();
	MX_ADC2_Init();
	MX_ADC1_Init();
	MX_I2C1_Init();
	MX_TIM17_Init();
	MX_USART3_UART_Init();
	MX_TIM3_Init();
	MX_TIM15_Init();
	MX_TIM16_Init();
	MX_TIM2_Init();
	/* USER CODE BEGIN 2 */
	//MOTOR A
	HAL_TIM_PWM_Start(&htim3, TIM_CHANNEL_3);
	HAL_TIM_PWM_Start(&htim3, TIM_CHANNEL_4);

	//MOTOR B
	HAL_TIM_PWM_Start(&htim2, TIM_CHANNEL_3);
	HAL_TIM_PWM_Start(&htim2, TIM_CHANNEL_4);
	//SERVO
	HAL_TIM_PWM_Start(&htim15, TIM_CHANNEL_1);
	HAL_TIM_PWM_Start(&htim15, TIM_CHANNEL_2);

	//OUTPUT IR SENSOR MODULE
	HAL_TIM_PWM_Start(&htim16, TIM_CHANNEL_1);

	/* USER CODE END 2 */

	/* Infinite loop */
	/* USER CODE BEGIN WHILE */
	while (1) {
		/* USER CODE END WHILE */

		/* USER CODE BEGIN 3 */
		send_string("Hello world!\r\n");

//HAL_Delay(1000);
		__HAL_TIM_SET_COMPARE(&htim3, TIM_CHANNEL_3, MOTOR_A);
		__HAL_TIM_SET_COMPARE(&htim3, TIM_CHANNEL_4, 0);

		__HAL_TIM_SET_COMPARE(&htim2, TIM_CHANNEL_3, MOTOR_B);
		__HAL_TIM_SET_COMPARE(&htim2, TIM_CHANNEL_4, 0);

		__HAL_TIM_SET_COMPARE(&htim15, TIM_CHANNEL_1, SERVO_A);
		__HAL_TIM_SET_COMPARE(&htim15, TIM_CHANNEL_2, SERVO_B);

		if(1==rising_flag_A )
		{
			SERVO_A += 1;
			MOTOR_A += 1;
		}
		else
		{
			SERVO_A -= 1;
			MOTOR_A -= 1;
		}
		if(1==rising_flag_B )
		{
			SERVO_B += 1;
			MOTOR_B += 1;
		}
		else
		{
			SERVO_B -= 1;
			MOTOR_B -= 1;
		}

		HAL_Delay(1);

		if (SERVO_A > 2000) {
			rising_flag_A = 0;

		}
		else if(SERVO_A < 1)
		{
			rising_flag_A = 1;
		}

		if (SERVO_B > 2000) {
			rising_flag_B = 0;

		}
		else if(SERVO_B < 1)
		{
			rising_flag_B = 1;
		}



	}
	/* USER CODE END 3 */
}

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


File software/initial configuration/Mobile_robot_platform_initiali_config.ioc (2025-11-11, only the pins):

Mcu.UserName=STM32G431RBTx
PA0.Signal=ADC2_IN1
PA1.Signal=ADC2_IN2
PA10.Signal=GPIO_Input
PA11.Signal=GPIO_Input
PA12.Signal=GPIO_Input
PA13.Signal=SYS_JTMS-SWDIO
PA14.Signal=SYS_JTCK-SWCLK
PA15.Signal=SYS_JTDI
PA2.Signal=ADC1_IN3
PA3.Signal=ADC1_IN4
PA4.Signal=COMP_DAC11_group
PA5.Signal=COMP_DAC12_group
PA6.GPIO_Label=LED_SENSOR_PWM
PA6.Signal=S_TIM16_CH1
PA7.GPIO_Label=STATUS_LED3
PA7.Signal=GPIO_Output
PA8.Signal=GPIO_Input
PA9.Signal=GPIO_Input
PB0.Signal=S_TIM3_CH3
PB1.Signal=S_TIM3_CH4
PB10.Signal=S_TIM2_CH3
PB11.Signal=S_TIM2_CH4
PB12.Signal=ADC1_IN11
PB13.Signal=GPIO_Input
PB14.GPIO_Label=Servo1
PB14.Signal=S_TIM15_CH1
PB15.GPIO_Label=Servo2
PB15.Signal=S_TIM15_CH2
PB2.GPIO_Label=V_VHK
PB2.Signal=ADC2_IN12
PB3.Signal=GPIO_Input
PB4.Signal=GPIO_Input
PB5.Signal=GPIO_Input
PB6.Signal=GPIO_Input
PB7.Signal=I2C1_SDA
PB8-BOOT0.Signal=I2C1_SCL
PB9.Signal=S_TIM17_CH1
PC0.Signal=ADC2_IN6
PC1.Signal=ADC2_IN7
PC10.Signal=USART3_TX
PC11.Signal=USART3_RX
PC12.Signal=GPIO_Input
PC13.GPIO_Label=KILL PIN
PC13.Signal=GPIO_Input
PC14-OSC32_IN.GPIO_Label=IR
PC14-OSC32_IN.Signal=GPXTI14
PC15-OSC32_OUT.GPIO_Label=STATUS_LED1
PC15-OSC32_OUT.Signal=GPIO_Output
PC2.Signal=ADC2_IN8
PC3.Signal=ADC2_IN9
PC4.GPIO_Label=STATUS_LED2
PC4.Signal=GPIO_Output
PC5.Signal=ADC2_IN11
PC6.Signal=GPIO_Input
PC7.Signal=GPIO_Input
PC8.Signal=GPIO_Input
PC9.Signal=GPIO_Input
PD2.Signal=GPIO_Input

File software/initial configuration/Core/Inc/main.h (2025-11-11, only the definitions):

#define KILL_PIN_Pin GPIO_PIN_13
#define KILL_PIN_GPIO_Port GPIOC
#define IR_Pin GPIO_PIN_14
#define IR_GPIO_Port GPIOC
#define STATUS_LED1_Pin GPIO_PIN_15
#define STATUS_LED1_GPIO_Port GPIOC
#define LED_SENSOR_PWM_Pin GPIO_PIN_6
#define LED_SENSOR_PWM_GPIO_Port GPIOA
#define STATUS_LED3_Pin GPIO_PIN_7
#define STATUS_LED3_GPIO_Port GPIOA
#define STATUS_LED2_Pin GPIO_PIN_4
#define STATUS_LED2_GPIO_Port GPIOC
#define V_VHK_Pin GPIO_PIN_2
#define V_VHK_GPIO_Port GPIOB
#define Servo1_Pin GPIO_PIN_14
#define Servo1_GPIO_Port GPIOB
#define Servo2_Pin GPIO_PIN_15
#define Servo2_GPIO_Port GPIOB

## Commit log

2025-11-11 initial release
    initial release
    [analogSensor.kicad_sch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]
2025-11-12 bug solving
    - DRC error solving related with I2C pull-up resistors
    - updating readme
    [mobile_robot-B_Cu.gbr, mobile_robot-B_Mask.gbr, mobile_robot-B_Paste.gbr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]
2026-04-27 update routing, changed IR sensor with pinout, rotate right sensor connector (bottom side)
    [mobile_robot.kicad_pcb, mobile_robot.kicad_sch]
2026-04-28 update GND routing
    [mobile_robot.kicad_pcb, mobile_robot.kicad_sch, powerSection.kicad_sch]
2026-04-28 update gerber files and STEP file
    [mobile_robot-B_Cu.gbr, mobile_robot-B_Mask.gbr, mobile_robot-B_Paste.gbr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]

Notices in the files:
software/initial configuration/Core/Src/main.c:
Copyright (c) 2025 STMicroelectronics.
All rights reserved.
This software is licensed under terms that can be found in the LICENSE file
